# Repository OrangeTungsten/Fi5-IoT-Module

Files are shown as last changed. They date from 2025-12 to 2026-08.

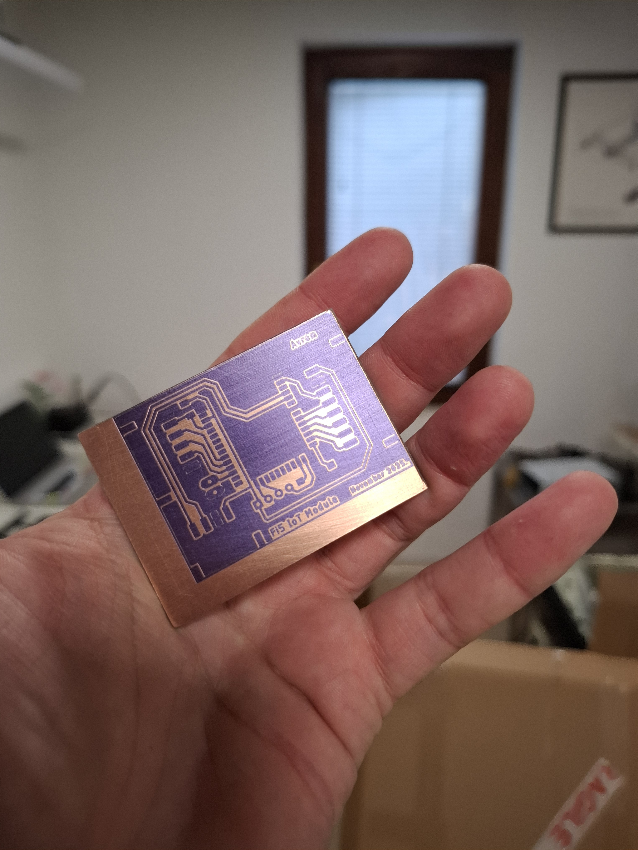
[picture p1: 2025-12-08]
PCB/Pictures/20251115_152900.jpg

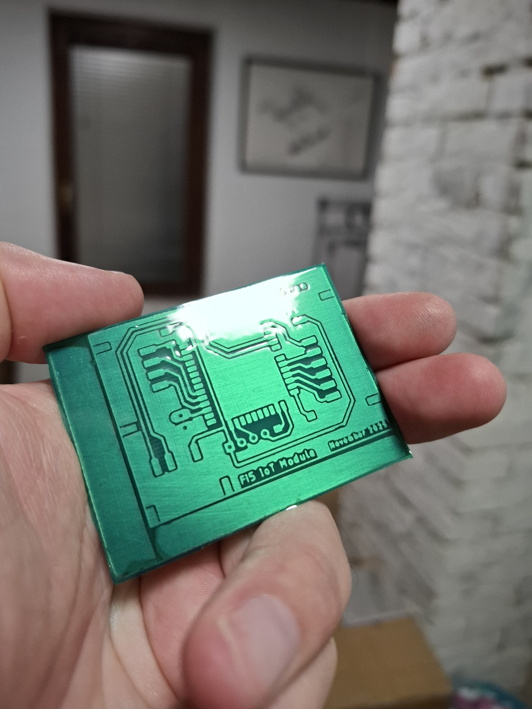
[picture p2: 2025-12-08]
PCB/Pictures/20251115_200205.jpg

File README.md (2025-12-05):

Baner

# Introduction

Fi5 IoT module is an ESP-32S-based device designed primarily as a data-logging unit, enabling the collection and upload of 3D printing statistic values to a cloud server, as well as displaying them locally on a dedicated display. The project also involves extending the Marlin project by adding a custom G-code command at the firmware level.

This version of the device is implemented on a [Flutur i5](https://github.com/OrangeTungsten/Flutur-i5) FDM 3D printer, with [MKS Robin Nano v1.2](https://makerbase3d.com/product/mks-robin-nano-v1-2/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) controller board running on a [Marlin v2.1.2.5](https://github.com/MarlinFirmware/Marlin/tree/2.1.2.5) firmware, but it can be connected to any other device as long as the system is capable of exchanging data over an available UART port. An MH-ET 2.13 in E-ink display is used for local output.

This project provides an infrastructure for communication with external devices, enabling the forwarding of selected data to a cloud server, forming an easily operable IoT platform that It can be used as a flexible platform for creating logging solutions of various types. Project is suitable for further development in multiple directions. The system can be expanded to support two-way communication, allowing remote-control functionality of connected device (3D printer). Although the device is currently implemented for one type of application – logging data, it can be upgraded to support different types of peripherals, including operation with multiple devices simultaneously. This infrastructure provides flexibility and openness for any type of future upgrade.

**Project provides:**
- Complete documentation for reproducing the device: Bill of materials; Electronics schematics; PCB layouts (copper, soldermask, and silkscreen layers); PCB build parameters and guidance; CAD models of 3D printable enclosure; Guidance for configuration;

- Additional code and guidance for modifying 3D printer firmware in order to define a new, UART communication port;

- Additional code and guidance for expanding Marlin firmware with a new g-code machine command;

- Additional code and guidance for creating cloud platform on Google Drive for storing data;

- Device firmware source code with guidance.

## Stages of realization

Project consists of five main stages of realization:

1. Establishing serial communication between devices;
2. Creating a custom G-code M command for sending data over the predefined UART port;
3. Extracting desired data on firmware level;
4. Creating a cloud platform;
5. Creating a device firmware.

------------------------------------------------------

# 1. Establishing serial communication between devices

A 3D printer motherboard can exchange data with other devices through communication interfaces such as UART, I²C, SPI, CAN, or USB. Each of these interfaces is a built-in hardware feature of the microcontroller, and they follow specific communication protocols (rules for how data is sent and received). Depending on the hardware and firmware configuration, these interfaces can be assigned to certain pins on the board. An interface, once mapped to specific physical pins, constitutes a communication port. Through these ports, the control board can reliably talk to external devices (modules). A lot of microcontrollers (therefore motherboards) have multiple ports, used for different purposes.
All modern 3D printer motherboards include a dedicated communication port for connecting to a host computer. At the microcontroller level, this port is typically implemented as a UART interface, which is then bridged through a USB-to-UART converter (such as CH340, CP2102, or FT232) and exposed to the computer as a standard USB serial port. This port serves as the primary channel for host communication, allowing direct control, firmware configuration, and interactive G-code exchange (control via Pronterface i.e.).
The idea is to create a device that communicates with the microcontroller of the 3D printer motherboard over an another available UART port, independent of the port used for communication with the computer. The device will wait for messages, process them and forward desired data to the cloud – a predefined internet service.

## UART
Universal Asynchronous Receiver/Transmitter (UART) is a simple serial communication interface used to send data between two digital devices using only one transmit and one receive line (TX and RX). Unlike parallel communication where several bits are transferred at once, UART sends data bit-by-bit over a single wire, making it cost-effective, low-pin and easy to implement. Data is framed with a start bit, optional parity, and stop bit, so both sides understand where each byte begins and ends. Because UART is asynchronous, both devices must use the same baud rate (bit speed) to correctly interpret the data, but no shared clock line is needed.
##Port on motherboard
MKS Robin Nano v1.2 is running on [STM32F103VET6](https://www.st.com/en/microcontrollers-microprocessors/stm32f103ve.html) microcontroller. Official documentation shows that this microcontroller features up to five UART interfaces. USART ports also support synchronous mode, which is not needed for this application.

Table 1. shows the default pinout:

| Peripheral | TX | RX |
| --- | ---- | ---- |
| USART1 | PA9  | PA10 |
| USART2 | PA2  | PA3  |
| USART3 | PB10 | PB11 |
| UART4 | PC10 | PC11 |
| UART5 | PC12 | PD2  |

On STM32F1 devices, the USART/UART peripherals can be reassigned to alternative pin sets using the AFIO remap functionality, but in this project only the default (reset state) pin assignments are considered because the 3DP motherboard already has the remaining pins allocated to other functions and features.
By reviewing the MKS Robin Nano V1.2 motherboard documentation and the Marlin 2.1.2.5 firmware, it was observed that all default UART pins are already used by existing system features. The only UART interface that can be utilized without compromising system integrity or requiring additional remapping is USART1 (TX/RX: PA9/PA10), which is assigned to the optional wireless module port on the motherboard.

The following code is done on firmware of 3D printer’s microcontroller.

## Defining available port on 3DP firmware level

Following files should be edited/created:

edit: Marlin/Configuration.h

```cpp
#define IOT_MODULE

#if ENABLED(IOT_MODULE)
  //IoT module could be enabled only if MKS_WIFI_MODULE is disabled
  #if ENABLED(MKS_WIFI_MODULE)
    #error "Can't use IOT_MODULE module if MKS_WIFI_MODULE is enabled."
  #else
    #define IOT_MODULE_PORT 1 //Which UART port custom ESP IoT module will use. i.e. 1 = UART1(Tx-PA9;Rx-PA10)
    #define IOT_MODULE_BAUDRATE 115200
  #endif
#endif
```

create: Marlin/src/core/serial_extension.h
```cpp
#include "serial.h"

//Define Universal Serial call
#define _SERIAL_PORT_IOT(N)  Serial##N
#define  SERIAL_PORT_IOT(N)  _SERIAL_PORT_IOT(N) 

//Define Serial println function for new port
#define SERIAL_IOT_PRINT(P)   SERIAL_PORT_IOT(IOT_MODULE_PORT).print(P)
#define SERIAL_IOT_PRINTLN(P) SERIAL_PORT_IOT(IOT_MODULE_PORT).println(P)
```

edit: Marlin/src/MarlinCore.cpp

```cpp
#if ENABLED(IOT_MODULE)
  #include "core/serial_extension.h"
#endif
```

edit: Marlin/src/MarlinCore.cpp > setup()
```cpp
SERIAL_PORT_IOT(IOT_MODULE_PORT).begin(IOT_MODULE_BAUDRATE);
```
Now, a new, dedicated, serial port called SERIAL_PORT_IOT is defined. Marlin has a built-in pin allocation functionality, so it is sufficient to define new port by its numerical identifier (1), rather than by  specifying  the physical pins names or addresses. The remaining configuration is already handled in the Wserial.h and HardwareSerial.h files.

----------------------------------------------------------------------------------

## 2. Creating a custom g-code M command for sending data over the SERIAL_PORT_IOT

New command will be executed via M1600 call. A new file called M1600.cpp should be created, and existing gcode.h and gcode.cpp files should be edited:

edit: Marlin/src/gcode/gcode.h > GcodeSuite

```cpp
  #if ENABLED(IOT_MODULE)
    static void M1600();
  #endif
```

edit: Marlin/src/gcode/gcode.cpp > process_parsed_command(const bool) > switch (parser.command_letter) > case 'M': switch (parser.codenum)

```cpp
  #if ENABLED(IOT_MODULE)
    case 1600: M1600(); break;
  #endif
```

create: Marlin/src/gcode/IoT/M1600.cpp

```cpp
#include "../../MarlinCore.h"
#include "../../inc/MarlinConfig.h"

#if ENABLED(IOT_MODULE)
    
    #include "../gcode.h"
    #include "../../core/serial_extension.h"
    
    void GcodeSuite::M1600() {

        SERIAL_IOT_PRINT(/*Here goes String type message*/);

    }

#endif
```

--------------------------------------------

#3. Extracting desired data on firmware level

Marlin firmware has a built-in software module called "printcounter", which should be enabled in the *configuration.h* file 

edit: Marlin/Configuration.h

```cpp
#define PRINTCOUNTER
#if ENABLED(PRINTCOUNTER)
  #define PRINTCOUNTER_SAVE_INTERVAL 0 // (minutes) EEPROM save interval during print. A value of 0 will save stats at end of print.
#endif
```

Given module records data like: total prints, runtime, failed prints and filament used and stores it into separate variables. The task is to forward this data to the new SERIAL_PORT_IOT serial port, where it will be received by the IoT module.

Marlin/src/module/printcounter.cpp has variables:

```cpp
struct printStatistics {    // 16 bytes
  //const uint8_t magic;    // Magic header, it will always be 0x16
  uint16_t totalPrints;     // Number of prints
  uint16_t finishedPrints;  // Number of complete prints
  uint32_t printTime;       // Accumulated printing time
  uint32_t longestPrint;
...
```

edit: Marlin/src/gcode/IoT/M1600.cpp

```cpp
#include "../../MarlinCore.h"
#include "../../inc/MarlinConfig.h"

#if ENABLED(IOT_MODULE)
    
    #include "../gcode.h"
    #include "../../core/serial_extension.h"
    #include "../../module/printcounter.h"

    printStatistics localStats;
    
    void GcodeSuite::M1600() {

        PrintCounter::init();

        localStats = PrintCounter::getStats();

        SERIAL_IOT_PRINT(localStats.totalPrints);
        SERIAL_IOT_PRINT(",");
        SERIAL_IOT_PRINT(localStats.finishedPrints);
        SERIAL_IOT_PRINT(",");
        SERIAL_IOT_PRINT(localStats.printTime );
        SERIAL_IOT_PRINT(",");
        SERIAL_IOT_PRINTLN(localStats.filamentUsed);

    }

#endif
```

Every time when M1600 command is called, message from 3DP motherboard will be sent over its UART1 port, in the form of single string line, where variables are separated with a separators (commas). In order to activate this system after every print, line M1600 should be placed at the end of every G-code (print). That should be done in the slicer configuration.
Later, firmware of the ESP32 (IoT Module) will be programmed to parse these values between separators to the separate variables.

----------------------------

# 4. Creating a cloud backend

In this setup, Google Drive, together with Google Spreadsheets and Apps Script, serves as a cloud backend for IoT data. It functions as a centralized repository where statistics from a 3D printer are periodically uploaded, and made available for further processing or download.
Functionality of this approach reflects in following: IoT module (device) sends HTTP POST request, triggering Google Apps Script webhook to append new rows to Google Sheet. Google Spreadsheet acts as a centralized cloud data store. Apps Script could be expanded to validate data, compute summaries, generate alerts, or create and update visualizations. 

## Procedure

The following procedure explains how to turn a Google Spreadsheet into a REST endpoint that accepts incoming HTTP requests from an ESP32 (or any HTTP client) and logs values into the sheet:

**1. Create a Google Spreadsheet**

Create a new Google Spreadsheet in your Google Drive. Rename current sheet into “Stats”. Add columns representing the parameters/data you plan to submit (optional). In this case columns: Total prints; Successful prints, Runtime; Filament used will be used.

**2. Create a Google Apps Script**

Open the Google Sheet → Extensions > Apps Script. Write a following script that will accept HTTP requests (POST or GET) and append rows into the sheet.

Code.gs

```js
function doPost(e) {

  //Catch data from POST request (JSON format)
  var data = JSON.parse(e.postData.contents);
  
  // Open Sheet (current file)
  var sheet = SpreadsheetApp.getActiveSpreadsheet().getSheetByName("Stats");
  
  //Make type with given format
  var row = [
    new Date(),         
    data.tP || "",    
    data.sP || "",   
    data.rT || "",
    data.fU || ""     
  ];
  
  //Append new row
  sheet.appendRow(row);

  //Return answer
  return ContentService
    .createTextOutput(JSON.stringify({status: "success", message: "Data stored"}))
    .setMimeType(ContentService.MimeType.JSON);
}

function doGet(e) {
  var sheet = SpreadsheetApp.getActiveSpreadsheet().getSheetByName("Stats");
  var lastRow = sheet.getLastRow();
  var lastTimestamp = sheet.getRange(lastRow, 1).getValue(); // 1 = first column

  //Return JSON answer
  return ContentService.createTextOutput(JSON.stringify({
    timestamp: lastTimestamp
  })).setMimeType(ContentService.MimeType.JSON);
}
```

**3. Deploy as Web App**

In the Apps Script editor, go to Deploy > New deployment, set “Who has access” to Anyone, then authorize and deploy the script. The generated URL becomes a write endpoint (REST API). By using this URL, any internet-connected device can read and write data to the spreadsheet (according to the defined Code.gs script).

**4. Test the endpoint**

You can test the endpoint using Postman / Hoppscotch / ReqBin:

Method: POST | Content-Type: application/json

Body example:
```
{
"tP" : 6, 
"sP" : 5,
"rT" : 36,
"fU" : 30
}
```

You should receive this response:

```
{
    "status": "success",
    "message": "Data stored"
}
```

And a new row should be added in the Stats sheet.

Snimak ekrana 2025-11-07 210756

# Device firmware
The device’s main task is to read message from the UART Serial2 port, parse the message into separate variables, process the values and forward them to the cloud service via POST request. The device also includes a user-defined settings like Wi-Fi and Endpoint URL configuration. These parameters can be set via the UART Serial0 port. Since the device uses a standalone ESP-32S module, a USB to UART bridge must be used for programming and later communication with computer. ESP32 programmer is recommended.

Access to settings and MCU reset function is provided via physical pushbuttons: RESET; IOT_CFG; WIFI_CFG; WIFI_RST. Settings are available all the times except except during message reading, cloud upload, and display update operations. The pushbuttons trigger interrupt events on the ESP-32S module, flagging input event during the run.

Firmware development was carried out using the PlatformIO ecosystem, with Arduino framework, acting as a hardware abstraction layer (HAL).

This firmware uses GxEPD2_3C with Adafruit BusIO and Adafruit GFX libraries for E-ink display control and ArduinoJson library for manipulating JSON data.

Firmware follows a simplified algorithms: 

main
wifi_cfg 
wifi_rst
url_cfg

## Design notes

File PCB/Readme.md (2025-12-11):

This document provides a complete overview of the device’s hardware interface and explains the steps required for proper configuration. It includes annotated images showing the pinout, detailed descriptions of each connector and button, as well as the full procedure for the initial setup and operation.

## Pinout
On the image below, pinout of MainPCB is given. 

Device config 1

Device features ports:
- **BTN_PORT** (X1) - used for connecting four configuration pushbuttons (ButtonsPCB peripheral);
- **3DP_PORT** (X2) - used for communication with 3D printer
- **PC_PORT** (X3) - used for connecting computer via UART to USB converter
- **DISP_PORT** (X4) - used for the E-ink display pheripheral

Flashing firmware and communication with PC is done via PC_PORT. USB-to-UART converter should be used. Use of [ESP32 programmer](https://www.aliexpress.com/item/1005009724924926.html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) is recommended.
Device features a programming button FLASH_BTN (SW1), which should be activated during the upload.

BTN_PORT (X1) is used for connection with ButtonsPCB

ButtonsPCB_Config

ButtonsPCB contains four pushbuttons used for defice configuration:
- **ESP_RST** (SW1)  - MCU reset
- **URL_CFG** (SW2)  - Defining URL for cloud service
- **WIFI_CFG** (SW3) - Wi-Fi connection configuration
- **WIFI_RST** (SW4) - Disconnecting from the current Wi-Fi network -> another click: deleting default Wi-Fi paarameters from the NVS.

Wi-Fi configuration should be done in communication with PC via PC_PORT.

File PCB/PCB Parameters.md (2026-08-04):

This document provides parameters for DIY PCB build. Manufacturing files are given.

## PCB clad
One sided PCB clad  
Copper thickness: 35 um  
Isolation thickness:  0.8 mm
___

## Exposure
Method: Photolithography on dry UV-sensitive film  
[UV film](https://www.aliexpress.com/item/1005001847878963.html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) warm laminated on clean copper layer  
Exposure method: Direct imaging using monochrome Stereolithography LCD  
Device: Anycubic Photon Mono M5s Pro  
Display type: Monochrome 10.1" LCD, UV light @ 405 nm  
Image used: Positive STL model of PCB traces  
Exposure mode: Single-frame light exposure  
Exposure time: 25 seconds  
___

## Developing
Solution: 1 mass% Na2Co3  
Temperature: 25 °C  
Agitation: Light scrubbing with soft brush  
___

## Etching
Solution: 40 mass% FeCl3 | pH = 1  
Temperature 55 °C  
Agitation: Horizontal cyclical motion with 80 strokes/min  
___

## Soldermask
Method: Dry-film UV curing soldermask  
Soldermask type: [Dynamask 5000](https://www.ebay.com/itm/285613425122) | Warm laminated on clean copper layer  
Photomask: Positive image of soldermaks-free positions  
Photomask material: OHP transparent foil | thickness = 100 um  
Printer: HP MFP-178 | HQ BW mode  
UV lamp: 4x 9 W U-Shaped UV bulbs @ 365 nm  
Exposure time: 60 s  
Developing: Same as PCB UV film | 1 mass% Na2Co3 @ 25 °C and light scrubbing with soft brush  
Final exposure time: 1h  
___

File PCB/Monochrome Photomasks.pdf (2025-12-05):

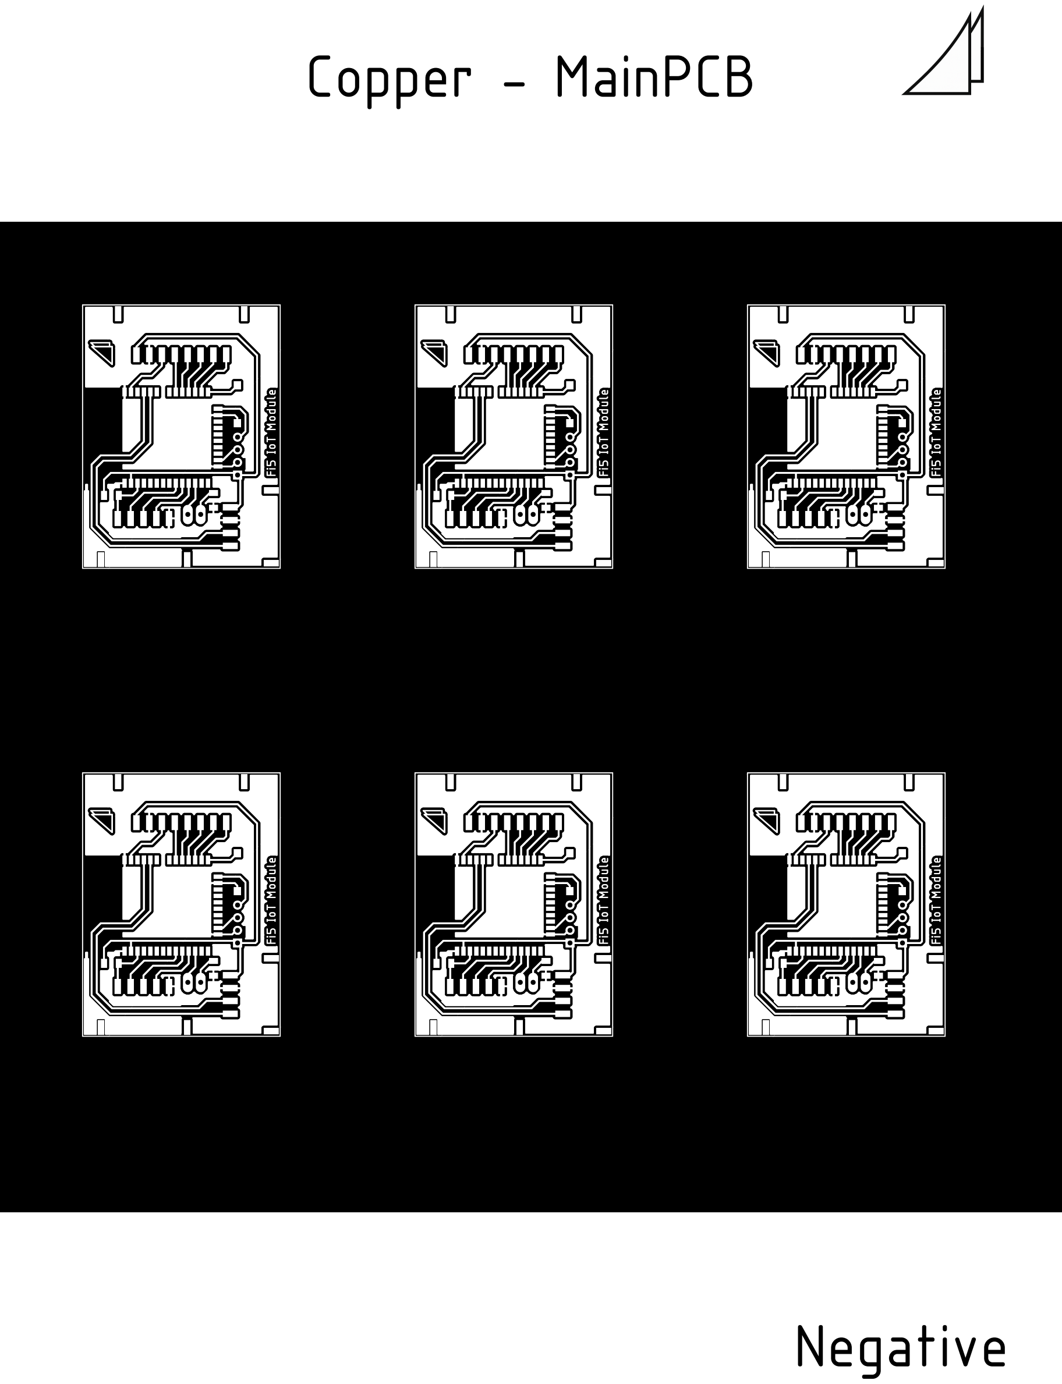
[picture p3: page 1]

Copper - MainPCB

Negative

Soldermask - MainPCB

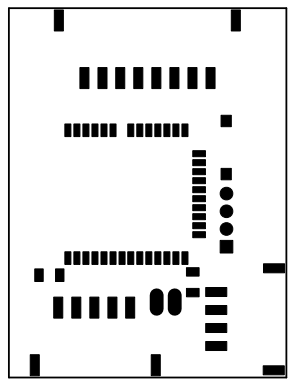
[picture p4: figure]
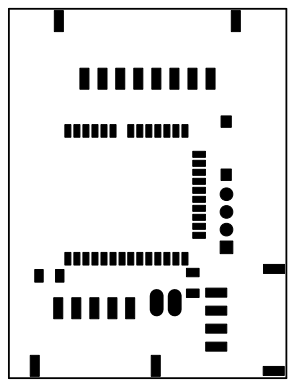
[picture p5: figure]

Positive

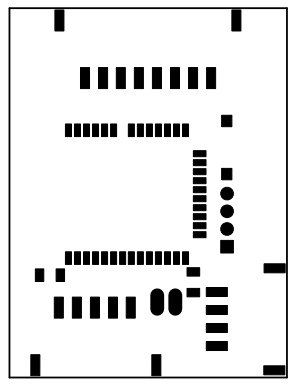
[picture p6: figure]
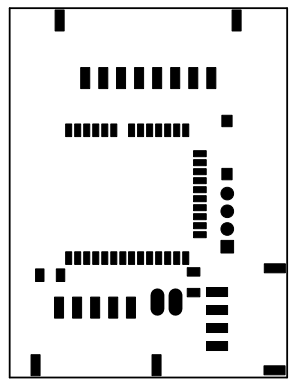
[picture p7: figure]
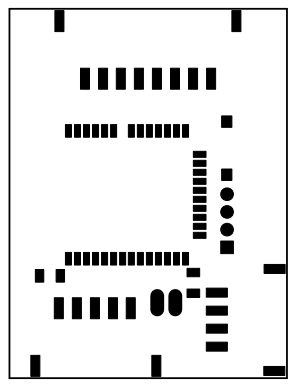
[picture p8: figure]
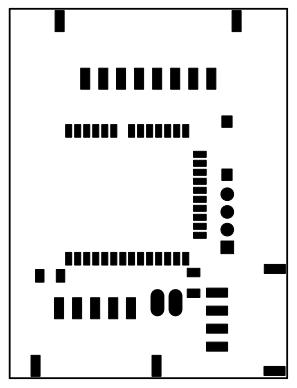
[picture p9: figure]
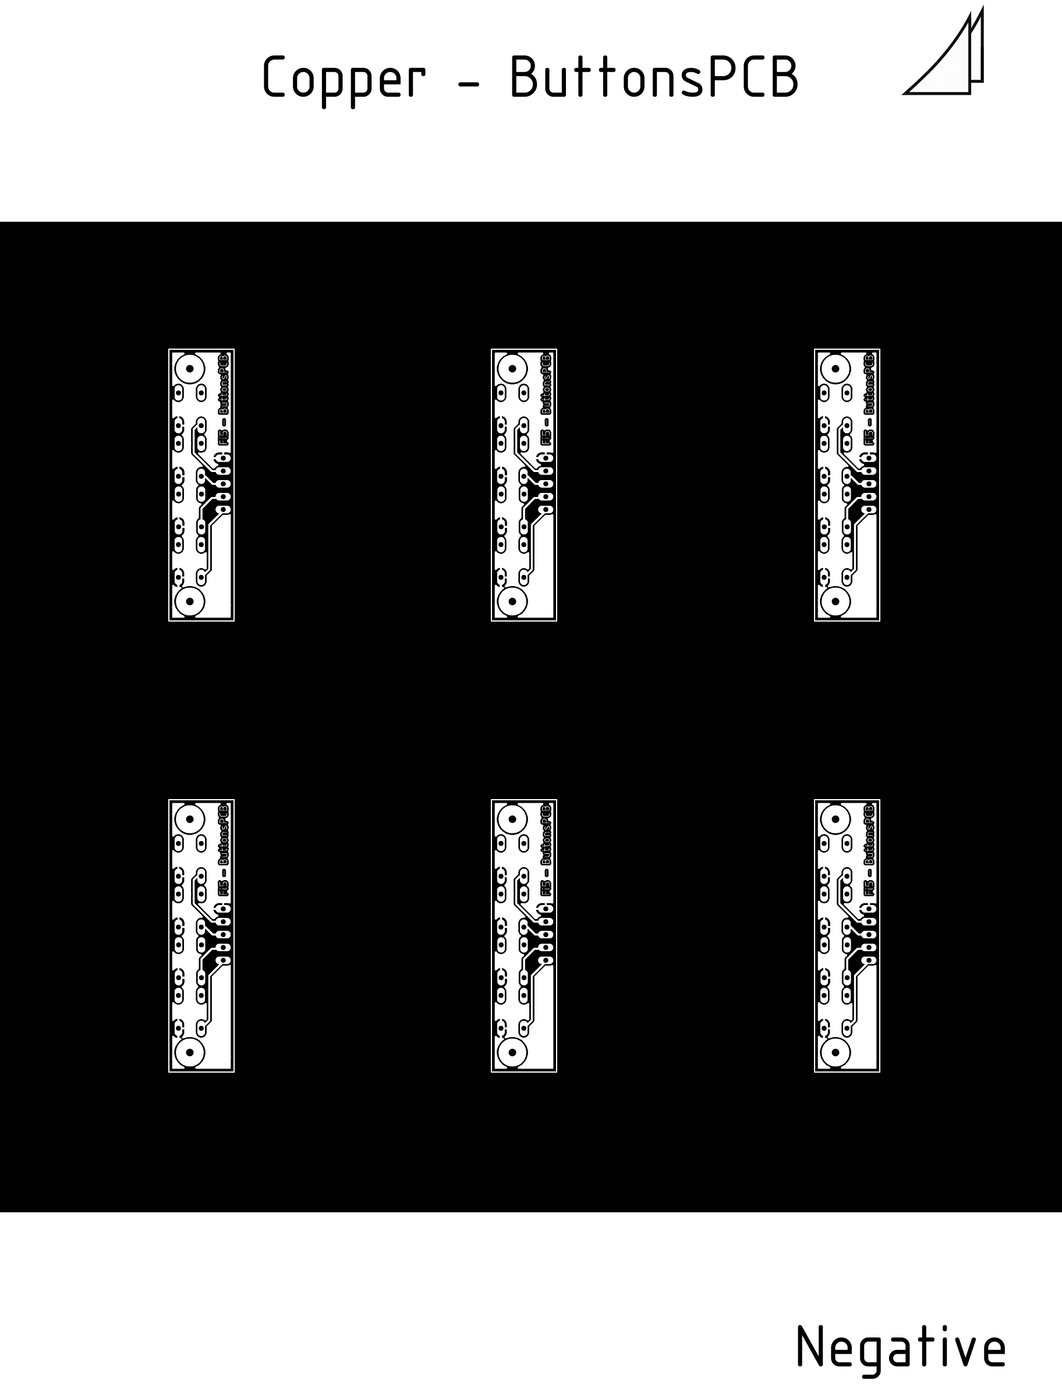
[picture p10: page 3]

Copper - ButtonsPCB

Negative

Soldermask - MainPCB

Positive

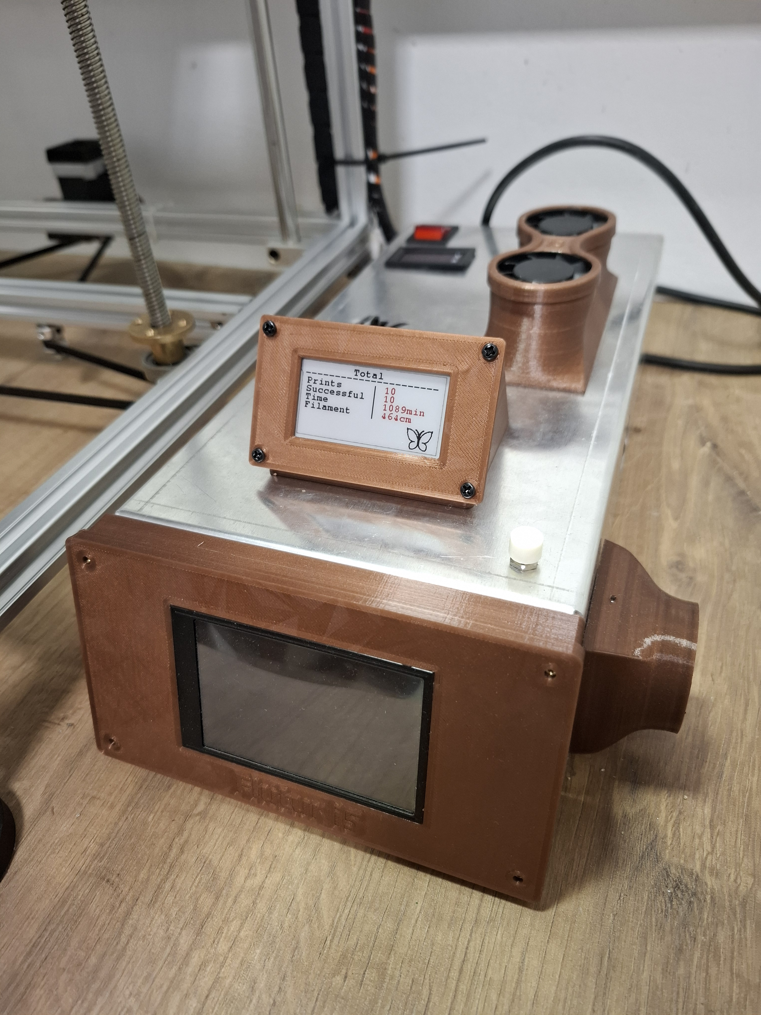
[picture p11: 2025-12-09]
Device.jpg

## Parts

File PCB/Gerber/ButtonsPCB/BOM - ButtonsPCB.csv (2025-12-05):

Qty | Value | Device | Package | Parts | Description | MF
1 |  | MA05-1 | MA05-1 | SV1 | PIN HEADER
1 | ESP_RST_BTN | 10-XX | B3F-10XX | SW1 | OMRON SWITCH
1 | URL_CFG_BTN | 10-XX | B3F-10XX | SW2 | OMRON SWITCH
1 | WIFI_CFG_BTN | 10-XX | B3F-10XX | SW3 | OMRON SWITCH
1 | WIFI_RST_BTN | 10-XX | B3F-10XX | SW4 | OMRON SWITCH

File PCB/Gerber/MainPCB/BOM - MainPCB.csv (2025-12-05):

Qty | Value | Device | Package | Parts | Description
1 | 04-2.54-B4B-XH-A | 04-2.54-B4B-XH-A | 4PIN | X3 | JST CONNECTOR
1 | 04-JST-B4B-XH-A | 04-JST-B4B-XH-A | 4PIN | X2 | JST CONNECTOR
1 | 05-2.54-B5B-XH-A | 05-2.54-B5B-XH-A | 5PIN | X1 | JST CONNECTOR
1 | 08.02.1954 | 08.02.1954 | 8PIN | X4 | JST CONNECTOR
1 | 10k | R_CHIP-1206(3216-METRIC) | RESC3216X70 | R1 | Resistor Fixed - Generic
1 | 330R | R_CHIP-1206(3216-METRIC) | RESC3216X70 | R2 | Resistor Fixed - Generic
1 | ESP-32S | ESP-32S | ESP32S | IC
1 | KSS-2EG4430 | KSS-2EG4430 | KSS-2EG4430 | SW1 | Size: 3x6mm
1 | MA02-1 | MA02-1 | MA02-1 | LED

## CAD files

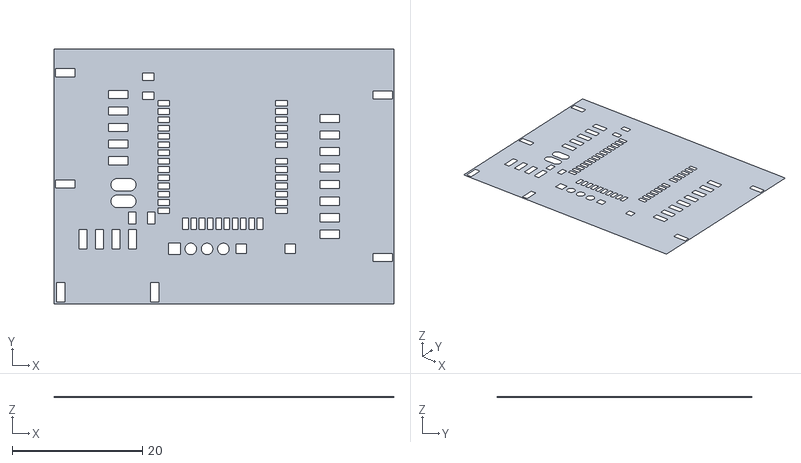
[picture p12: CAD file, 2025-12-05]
PCB/SLA/Soldermask - MainPCB.stl
52.2 x 39.1 x 0.0804

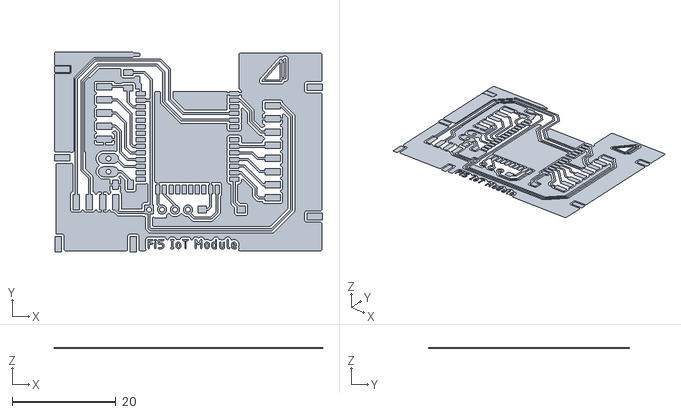
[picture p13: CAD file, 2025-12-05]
PCB/SLA/Copper - MainPCB.stl
51.7 x 38.6 x 0.035

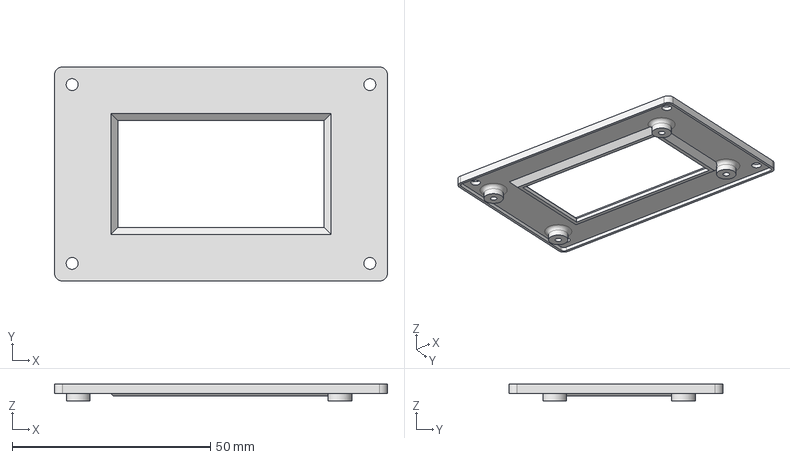
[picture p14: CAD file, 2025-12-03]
Housing/STEP/Fi5 Housing Lid.stp
84.0 x 54.0 x 4.20 mm

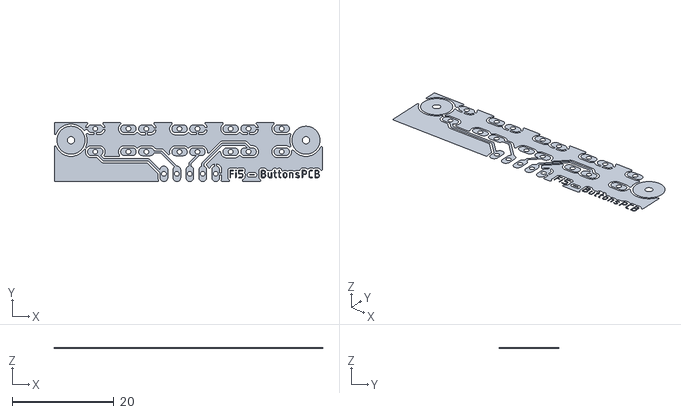
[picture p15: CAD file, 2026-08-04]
PCB/SLA/Copper - Buttons PCB.stl
52.6 x 11.6 x 0.035

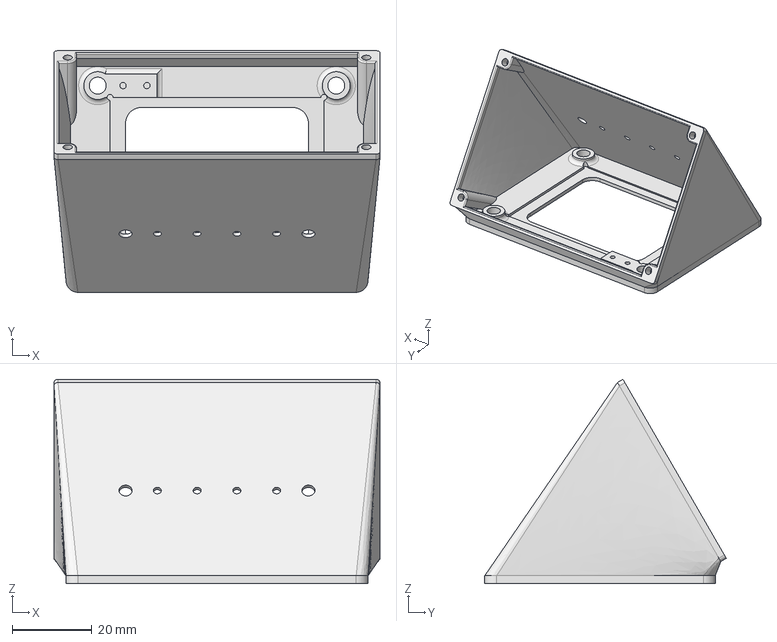
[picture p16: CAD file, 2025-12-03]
Housing/STEP/Fi5 Housing Base.stp
82.0 x 60.8 x 51.4 mm

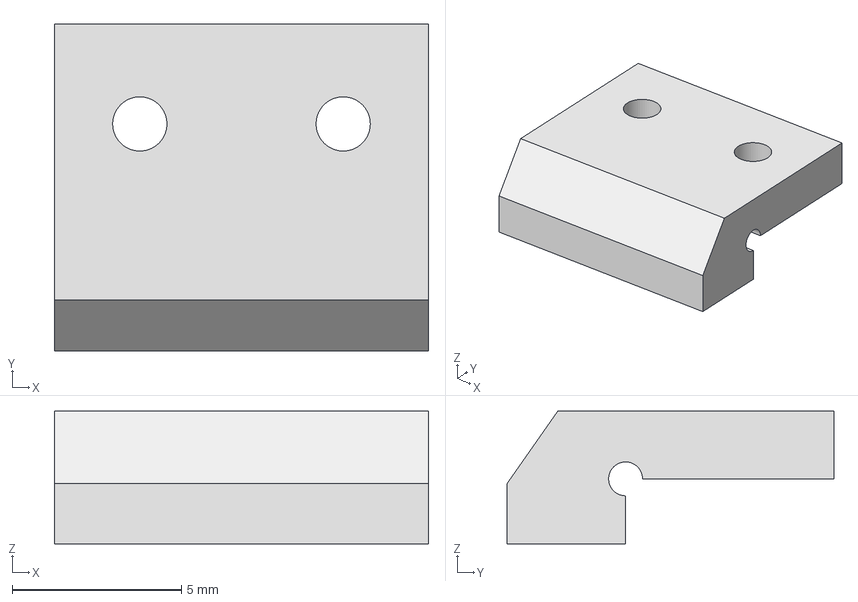
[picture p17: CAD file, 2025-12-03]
Housing/STEP/Fi5 Housing Clamp.stp
11.0 x 9.65 x 3.92 mm

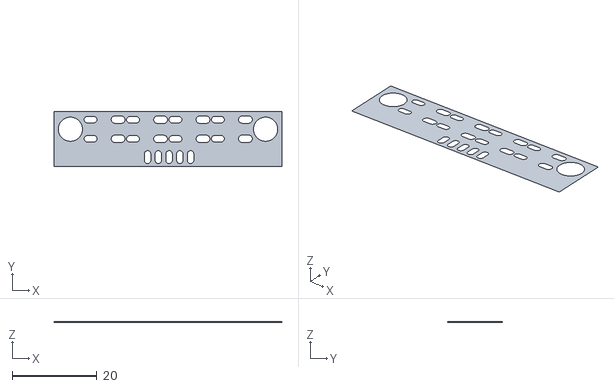
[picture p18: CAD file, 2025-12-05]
PCB/SLA/Soldermask - ButtonsPCB.stl
53.8 x 12.9 x 0.0804

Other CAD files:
Housing/STL/Fi5 Housing Base.stl
Housing/STL/Fi5 Housing Clamp.stl
Housing/STL/Fi5 Housing Lid.stl

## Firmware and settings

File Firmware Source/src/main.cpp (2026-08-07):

/*
 * main.cpp
 * Fi5-IoT-Module — ESP32-based IoT and Logging Module
 *
 * Project: Fi5-IoT-Module | https://github.com/OrangeTungsten/Fi5-IoT-Module
 * Parent project: Flutur-i5 3D printer | https://github.com/OrangeTungsten/Flutur-i5
 *
 * Description:
 *   This file contains the main code for the Fi5-IoT-Module,
 *   an ESP32-powered system designed to collect, process, and transmit
 *   operational data from 3D printers or other serial-based devices.
 *   The module listens on a UART interface, parses incoming telemetry
 *   (e.g., print counters, runtime statistics, filament usage), and
 *   optionally forwards the processed data to a cloud backend or displays
 *   it locally.
 *   This module is hardware-agnostic and can be adapted to different printer firmwares.
 *   Refer to README.md and PCB/Readme.md for details, pinout and wiring diagrams.
 *
 * Author: OrangeTungsten
 * Created: August 2025
 * Last Modified: 15.08.2026.
 *
 * License: GPL-3.0 (refer to the LICENSE file in this repository)
 *
 */


#include <Arduino.h>
#include <nvs_flash.h>
#include <Preferences.h>
#include "Configuration.h"
#include "Connection_Module/WiFi_Module.h"
#include "Display_Module/Display_Module.h"
#include "IoT_Module/IoT_Module.h"


Preferences EEPROM;

volatile bool WIFI_CFG = 0;
volatile bool WIFI_RST = 0;
volatile bool URL_CFG  = 0;

String WriteAPI, dateTime;
String totalPrints, failedPrints, printTime, filamentUsed;

extern WiFiParameters Parameters;


void IRAM_ATTR WiFiCfgISR();
void IRAM_ATTR WiFiRstISR();
void IRAM_ATTR IoTCfgISR();

void EstablishNewConnection();
void EstablishOldConnection();
void WiFiReset();
void SaveNewParameters();
void DefineEndpointURL();
void getCurParams();

void RecordMessage(HardwareSerial &serialPort, char separator);
void UploadData(String tP, String fP, String pT, String fU);

void SerialPrintEndSession(char sign);



void setup() {

    //Initialize NVS (EEPROM)
    esp_err_t err = nvs_flash_init();
    if (err == ESP_ERR_NVS_NO_FREE_PAGES || err == ESP_ERR_NVS_NEW_VERSION_FOUND) {
        nvs_flash_erase();
        nvs_flash_init();
    }  

    EEPROM.begin("WiFi Parameters", RW_MODE);
    EEPROM.begin("API", RW_MODE);

    //Initialize display
    InitializeDisplay();
    
    //Initialize both Serial ports.
    Serial.begin(115200);
    Serial2.begin(115200, SERIAL_8N1, RXD2, TXD2);
        
    //Pin Mode
    pinMode(WIFI_CFG_PIN, INPUT_PULLUP);
    pinMode(WIFI_RST_PIN, INPUT_PULLUP);
    pinMode(IOT_CFG_PIN,  INPUT_PULLUP);
    pinMode(LED_PIN, OUTPUT);

    attachInterrupt(WIFI_CFG_PIN, WiFiCfgISR, FALLING);
    attachInterrupt(WIFI_RST_PIN, WiFiRstISR, FALLING);
    attachInterrupt(IOT_CFG_PIN,  IoTCfgISR,  FALLING);


    digitalWrite(LED_PIN, 0);
    SerialPrintEndSession('-');


    Serial.println("Checking for default parameters...");
    
    //Initial connection to existing WiFi
    if(EEPROM.isKey("SSID") && EEPROM.isKey("Password")){
        WiFiConnect(EEPROM.getString("SSID"), EEPROM.getString("Password"));
    }else{
        Serial.println("There are no default parameters.");
        EstablishNewConnection();
    }

    //Check if API is defined
    if(EEPROM.isKey("APIEndpoint")){
        Serial.printf("Write API URL is: %s\n", EEPROM.getString("APIEndpoint").c_str());
    }else{
        Serial.println("Write API URL is not defined. Run setup by pressing IoT_Cfg button and typing '1'.");
    }


    SerialPrintEndSession('-');

    Serial.flush();
    Serial2.flush();
    
    
}

void loop() {
    
    //Until the message arrives
    while(Serial2.available() == 0){

        //Wi-Fi Configure Interrupt
        if(WIFI_CFG == 1){

            EstablishNewConnection();
            SerialPrintEndSession('=');
            WIFI_CFG = 0;

        }

        //Wi-Fi Reset Interrupt
        if(WIFI_RST == 1){

            WiFiReset();
            SerialPrintEndSession('=');
            WIFI_RST = 0;

        }

        //URL Configure Interrupt
        if(URL_CFG == 1){

            DefineEndpointURL();
            SerialPrintEndSession('=');
            URL_CFG = 0;
        
        }
        
        delay(10);

    }
    

    RecordMessage(Serial2, ',');
    UploadData(totalPrints, failedPrints, printTime, filamentUsed);
    UpdateDisplay(totalPrints, failedPrints, printTime, filamentUsed, "");


    Serial.flush();
    Serial2.flush();

    delay(10);

}

//Flagging button presses
void IRAM_ATTR WiFiCfgISR() {  
    WIFI_CFG = 1;
}

void IRAM_ATTR WiFiRstISR(){
    WIFI_RST = 1;
}

void IRAM_ATTR IoTCfgISR(){
    URL_CFG = 1;
}


//Connect to the new WiFi network
void EstablishNewConnection(){

    //Set the parameters
    Parameters = WiFiConfig();
    
    //Try to connect only if all input parameters are valid
    if(Parameters.Valid == true){

        WiFiConnect(Parameters.WiFiSSID, Parameters.WiFiPassword);
        
        Serial.println();

        //If connection is established, save current parameters as defaults
        if(Parameters.Connected == true){
            Serial.println("New connection is established.");
            SaveNewParameters();
        //If error, try to connect to with prevoiusly saved parameters
        }else{
            Serial.println("New connection is not established.");
            EstablishOldConnection();
        }

    }else{
        Serial.println("New connection is not established.");
    }

    return;
    
}

//Connect to the previous WiFi network
void EstablishOldConnection(){

    //Connect to old network only if Default parameters in NVM exist
    if(EEPROM.isKey("SSID") && EEPROM.isKey("Password")){
        
        Serial.println();
        Serial.println("Trying to connect to previous network:");
        
        WiFiConnect(EEPROM.getString("SSID"), EEPROM.getString("Password"));

        if(Parameters.Connected == true){
            Serial.println("Old onnection is retrived.");
        }else{
            Serial.println("Error. Old onnection is not retrived either.");
        }

    }else{
        Serial.println("Default parameters doesn't exist. Not connected.");
    }
   
}


//Disconnect from the current network and earse default parameters 
void WiFiReset(){

    WiFiDisconnect();

    delay(750);

    //Delete default parameters from NVM?
    Serial.println();
    Serial.println("Press WIFI_RST_BTN again for earsing default parameters.");
    
    unsigned long timer = millis();

    while(millis()-timer < 3000) {

        if(digitalRead(WIFI_RST_PIN) == 0){

            while(digitalRead(WIFI_RST_PIN)==0) {}

            EEPROM.remove("SSID");
            EEPROM.remove("Password");

            Serial.println("-> Default parameters are earsed");
            return;

        }
        delay(50);
    }

    Serial.println("-> Default parameters are not changed.");

}

//Store new WiFi parameters to the EEPROM (NVS)
void SaveNewParameters(){

    //Update SSID to NVM
    if(EEPROM.isKey("SSID") != 1 || Parameters.WiFiSSID != EEPROM.getString("SSID")){
        EEPROM.putString("SSID", Parameters.WiFiSSID);
        Serial.println("Default SSID is updated.");
    }else{
        Serial.println("Default SSID not changed.");
    }

    //Update Password to NVM
    if(EEPROM.isKey("Password") != 1 || Parameters.WiFiPassword != EEPROM.getString("Password")){
        EEPROM.putString("Password", Parameters.WiFiPassword);
        Serial.println("Default password is updated.");
    }else{
        Serial.println("Default password not changed.");
    }

}

//Store API endpoint URL to the EEPROM (NVS)
void DefineEndpointURL(){
    
    Serial.println("Define full URL of the API endpoint: ");
    while(Serial.available() == 0){}
    
    //Obtain variable from the input
    String APIEndpoint = Serial.readStringUntil('\n');
    Serial.println(APIEndpoint);

    //Store new API Endpoint URL to NVM
    if(EEPROM.isKey("APIEndpoint") != 1 || APIEndpoint != EEPROM.getString("APIEndpoint")){
        EEPROM.putString("APIEndpoint", APIEndpoint);
        Serial.println("Default API endpoint URL is updated.");
    }else{
        Serial.println("Default API endpoint URL is not changed.");
    }


}


//Assign arrived data from printer to the four variables
void RecordMessage(HardwareSerial &serialPort, char separator){

    digitalWrite(LED_PIN, 1);

    String message = serialPort.readStringUntil('\n');
    message.trim();

    //Parsing to four String variables
    totalPrints = message.substring(0, message.indexOf(separator));
    
    failedPrints = message.substring(message.indexOf(separator) + 1, message.indexOf(separator, message.indexOf(separator) + 1));
    
    printTime = message.substring(message.lastIndexOf(separator, message.lastIndexOf(separator) - 1) + 1, message.lastIndexOf(separator));
    const char* printTimeChar = printTime.c_str();
    int printTimeInt = atoi(printTimeChar) / 60; //min
    printTime = String(printTimeInt);
    
    filamentUsed = message.substring(message.lastIndexOf(separator) + 1);
    const char* filamentUsedChar = filamentUsed.c_str();
    int filamentUsedInt = atoi(filamentUsedChar) / 100; //cm
    filamentUsed = String(filamentUsedInt);

    //Debug
    Serial.println("Received data:");
    Serial.println(totalPrints);
    Serial.println(failedPrints);
    Serial.println(printTime);
    Serial.println(filamentUsed);
    SerialPrintEndSession('.');

    digitalWrite(LED_PIN, 0);
}

//Upload desired data to the corresponding fields
void UploadData(String tP, String fP, String pT, String fU){

    if(Parameters.Connected == 1){

        if(EEPROM.isKey("APIEndpoint")){
            String endpointURL =  EEPROM.getString("APIEndpoint");
            httpPOST(endpointURL, tP, fP, pT, fU);
        }else{
            Serial.println("API Endpoint URL is not defined. Run setup by pressing IoT_Cfg button.");
        }
        
    }else{
        Serial.println("Can't upload. Internet connection doesn't exist.");
    }

}


void getCurParams(){

    Serial.println(EEPROM.getString("SSID"));
    Serial.println(EEPROM.getString("Password"));

    Serial.println(EEPROM.getString("SSID"));
    Serial.println(EEPROM.getString("APIEndpoint"));

}

//Print text divider
void SerialPrintEndSession(char sign){

    for(uint8_t i=0; i<28; i++){
        Serial.print(sign);
    }

    Serial.println();
}

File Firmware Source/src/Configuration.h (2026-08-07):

#pragma once

//Preferances modes
#define RO_MODE true
#define RW_MODE false

//Display type
#define DISP_E_INK


#ifdef DISP_E_INK

    //Display Pins
    #define DISP_BUSY_PIN   4
    #define DISP_RESET_PIN  16
    #define DISP_DC_PIN     17
    #define DISP_CS_PIN     5
    //SCLK-18; SDI-23

#endif

//WiFi Settings Pins
#define WIFI_CFG_PIN 25
#define WIFI_RST_PIN 26

//IoT Settings
#define IOT_CFG_PIN 33
  
#define TOTAL_PRINTS_FIELD 1
#define SUCCESSFULL_PRINTS_FIELD 2
#define TOTAL_TIME_FIELD 3
#define FILAMENT_USED_FIELD 4


//Second Serial port
#define RXD2 2  // UART2 RX pin
#define TXD2 13  // UART2 TX pin

#define LED_PIN 27

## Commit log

2025-11-24 Add PCB fabrication parameters documentation
    Documented parameters and processes for PCB fabrication including clad, exposure, developing, etching, and soldermask.
2025-11-24 Update PCB Parameters documentation with links
2025-11-25 Enhance README with UART message details and cloud backend
    Clarified the message format from the 3DP motherboard and added details on integrating M1600 command in G-code. Updated the section on creating a cloud backend with Google Drive and Apps Script.
2025-11-27 Enhance device configuration documentation
    Added detailed sections on pinout and device features.
2025-11-27 Update Device config.md
2025-12-05 Clarify device firmware description in README
2025-12-08 Clarify device port usage and programming details
    Updated descriptions for device ports and programming instructions.
2025-12-08 added firmware
    [Configuration.h]
2025-12-08 pcb pics
2025-12-09 Revise document title and overview for clarity
    Updated the title and introduction of the document to focus on the device rather than just configuration.
